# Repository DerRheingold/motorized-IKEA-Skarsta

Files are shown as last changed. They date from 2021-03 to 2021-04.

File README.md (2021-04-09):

# motorized-IKEA-Skarsta

## The idea
The basic idea behind this was relatively simple: After the crank of my desk broke after a few months (the plastic part came lose) I wanted to motorize my Ikea Skarsta desk to automatically raise or lower by the press of a button. After a quick search I found two pages that inspired me and based on them I started putting the things together and modifying the code for the Arduino. As an added challenge: my desk isn't light. I got a water cooled desktop-PC sitting on it together with a Samsung 49" monitor. So I guess it's a total of 35-40 Kg that needs to be moved in total.

## Inspired by:
* http://cesarmoya.com/blog/motorizing-standup-desk/ (for most of the code and parts-list)
* https://github.com/aenniw/ARDUINO/tree/master/skarsta (for the 3d-printing layouts and the idea with sonar + 7-segment display hidden under a layer of 3D-print)

## The required parts (links to German shops):
* [Arduino Uno - 22€](https://www.exp-tech.de/plattformen/plattformen/arduino-plattform/mainboards/4380/arduino-uno-r3)
* [L298N Motor Driver - 4,50€](https://www.ebay.de/sch/i.html?_from=R40&_nkw=L298N&_sacat=0&rt=nc&LH_PrefLoc=1)
* [2 x 24v DC Motors (23kg.cm torque) - 41,65€/piece](https://www.exp-tech.de/motoren/dc-getriebemotoren/9878/50-1-metal-gearmotor-37dx70l-mm-24v-with-64-cpr-encoder-helical-pinion)
* [2 x L-Bracket for Motor - 6,50€](https://www.exp-tech.de/motoren/zubehoer-fuer-motoren/4857/pololu-stamped-aluminum-l-bracket-pair-for-37d-mm-metal-gearmotors)
* [24v 6A AC/DC Adapter - 17€](https://www.ebay.de/itm/Netzteil-Trafo-DC12-24V-2A-10A-Netzadapter-Driver-f-LED-Strip-Streifen-Notebook/224113909308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)
* [Sonar sensor - HC-SR04 - 3€](https://www.ebay.de/sch/i.html?_from=R40&_nkw=HC-SR04&_sacat=0&rt=nc&LH_PrefLoc=1)
* [TM1637 7-Segment-Display with 4 digits 0,56" - 3€](https://www.ebay.de/itm/TM1637-LED-4-Ziffern-7-Segment-Display-Uhr-Arduino-Raspberry/203030439344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)
* [2 x Motor Shaft Coupling (6mm to 7mm) - 3€/piece](https://www.ebay.de/sch/i.html?_from=R40&_nkw=Wellenkupplung+6mm&_sacat=0&rt=nc&LH_PrefLoc=1)
* 4x Push Buttons
* 8x 8mm washers
* 4x 10k OHM Resistors
* Barrel Jack to Cable adapter
* Junction Box
* Solderless Breadboard
* a hand full of jumper wires (Male-Female, as well as Male-Male)
* a friend with a 3D printer 😉
* some time to do metal working on the original drive shaft

Total cost ± 140€ depending on what small parts you have at home anyway.
Links to the shops are no ads, just to the parts I ordered and made some good experience with.

## The setup
Cut the crank apart if you want to, or use another 6mm allen wrench that you can get to fit. I recommend using a 7mm shaft coupling for easiest fit.

## The wiring
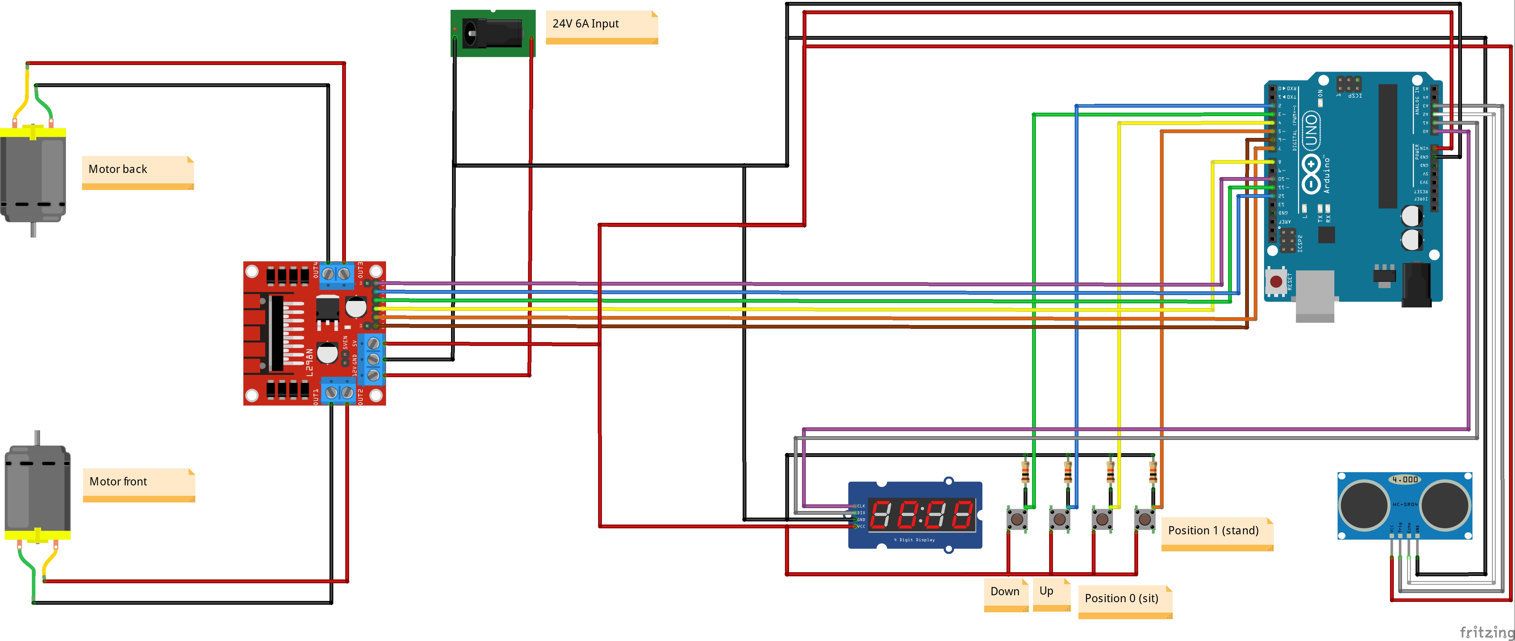
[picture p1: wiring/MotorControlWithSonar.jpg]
Wiring for the Ikea Skarsta project


## First run
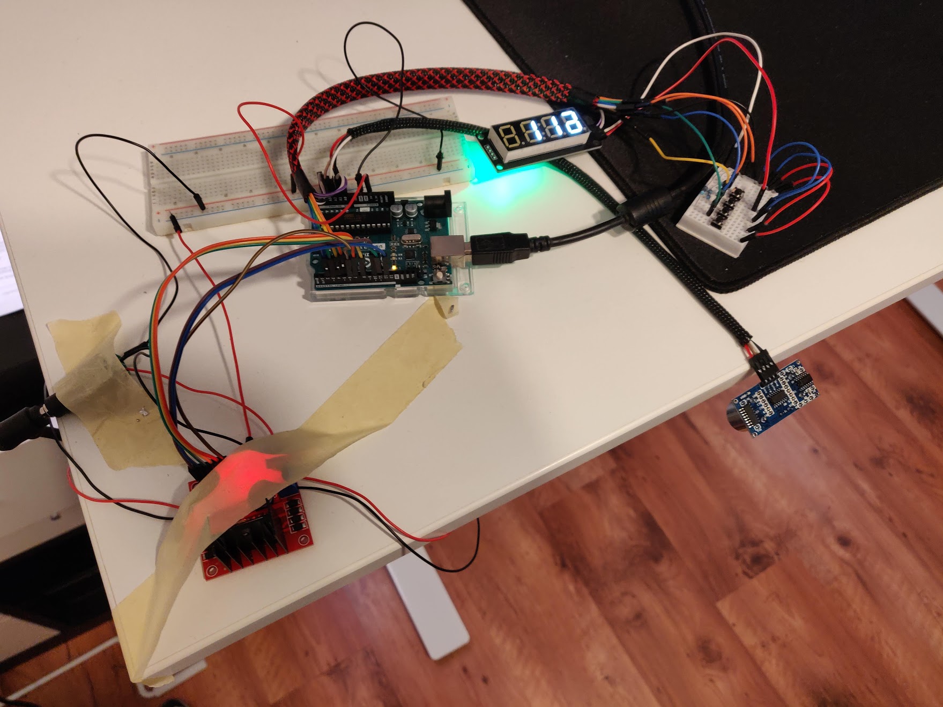
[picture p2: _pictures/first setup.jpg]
First setup of the system

Install everything outside of the desk first. When you're sure that everything is complete and the motors turn correctly install them under your desk. Make sure to measure trice and screw in only once 😉 Between the table and the L-Bracket holding the motors I installed 3mm washers to get the motor into the correct height aligned to the drive shaft. 

Once the motors are installed under the table, keep the wiring and Arduino-parts on the table to make a dry run. This will make debugging the software easier. Also Have a look at the Serial Monitor output when it's running, that might help finding errors too.

Remember to unplug the 5V-Pin in the arduino if you're running the external power to the peripherals and have the arduino plugged in to your PC via USB.

## 3D print
A friend and colleague of mine was so kind to assist my project when it came to the part of 3D printing. Based on the files provided he shortened the panel to house the display and 4 buttons: up, down, 0 and 1.

Also the housing for the sonar sensor was printed. Yes we could have made some housing to fit sonar, display and buttons in one pice. That's maybe something for a future update 😉

## Problems encountered and solved
* Voltage: First I tried with a 29V 2A power supply. This didn't provide enough "ompf" to let the motors drive the desk up. It only wen down 🙄 After upgrading to a 24V 6A power supply it worked fine. Though the L298N only outputs 18-19V to the motors the current is strong enough to power the motors. After all they are rated with 3A per motor :)
* NewPing: Initially it worked fine and just as intended. However when I didn't provide USB-power anymore but used an external power supply I constantly got errors. Turns out it's somewhat of [a known issue with newPing](https://arduino.stackexchange.com/questions/17406/ultrasonic-sensor-returns-random-values-on-external-power-supply). So I migrated to "Ultrasonic" which works fine now 😊

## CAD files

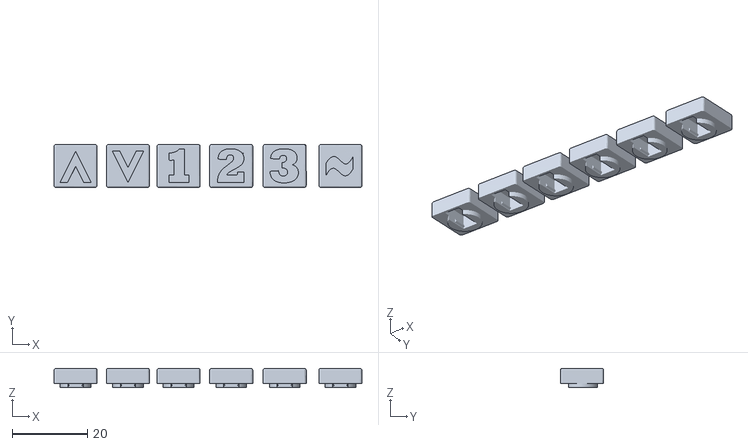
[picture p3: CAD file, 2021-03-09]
3d print/buttons.stl
82.0 x 11.5 x 5.17

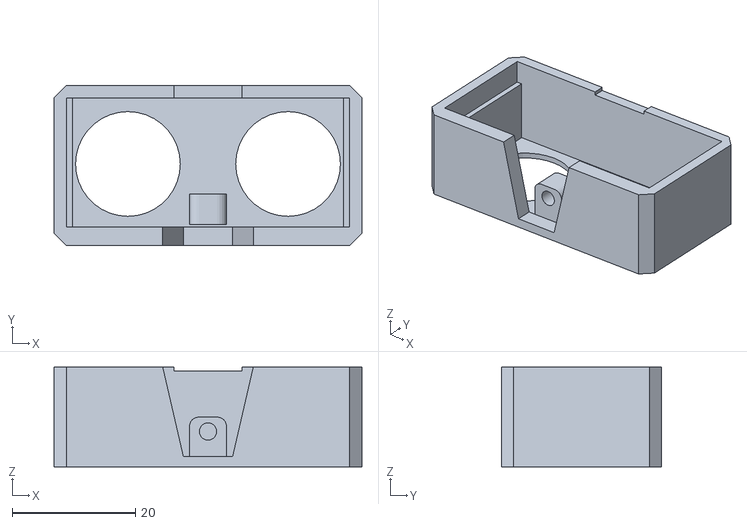
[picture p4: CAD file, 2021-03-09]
3d print/sonar-cap.stl
50.0 x 26.0 x 16.2

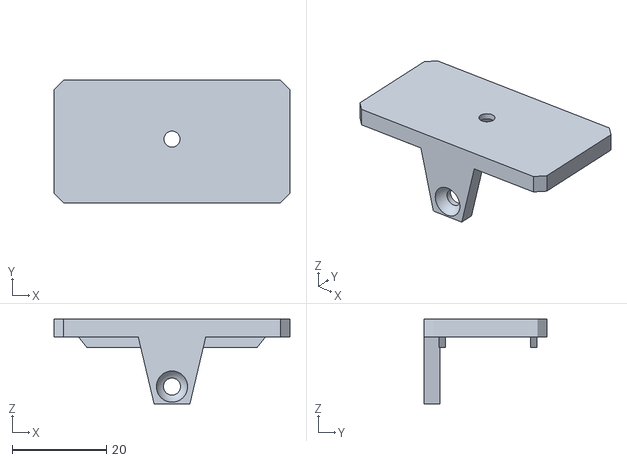
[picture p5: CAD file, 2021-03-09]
3d print/sonar-mount.stl
50.0 x 26.0 x 17.9

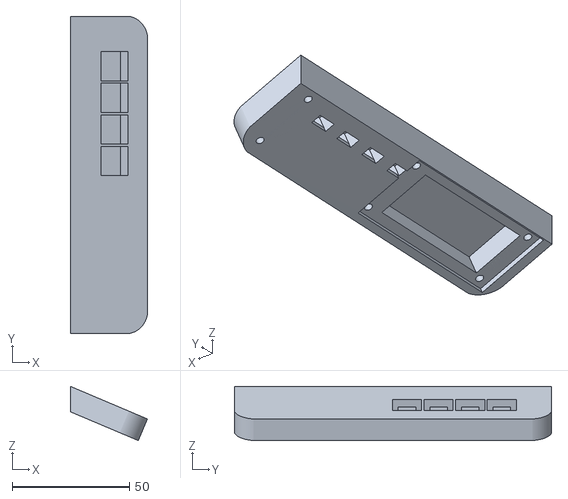
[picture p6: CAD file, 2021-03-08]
3d print/panel-cover-small.stl
32.9 x 135.4 x 23.1

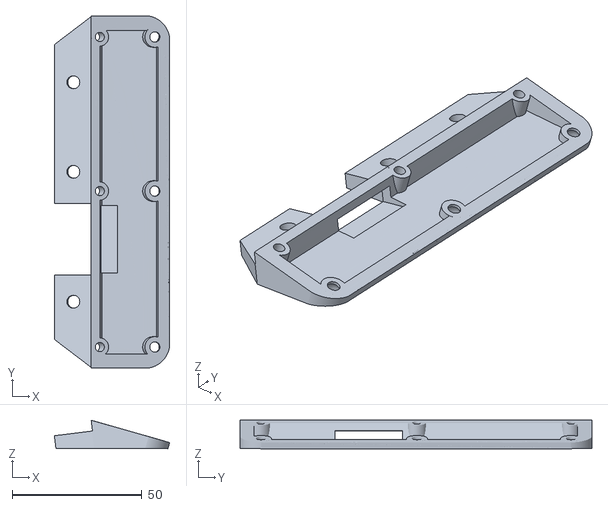
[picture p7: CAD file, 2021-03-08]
3d print/panel-bottom-small.stl
44.4 x 135.4 x 11.0

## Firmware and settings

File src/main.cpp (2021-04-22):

/*
  ----------------------------
   Arduino Power Desktop PLUS
  ----------------------------
  SUMMARY 
    Controls the direction and speed of the motor, supports auto-raising and auto-lowering by measuring the distance via sonar sensor
  
  DESCRIPTION 
    This code waits for a button to be pressed (UP or DOWN), and accordingly powers the motors in the desired direction and speed.
    One motor will turn clockwise, the other counterclockwise. The motors are intended to be placed facing each other, to duplicate the torque on the allen wrench
    On my particular setup (a heavy water cooled tower-PC and one 49" monitor totaling around 35-40 kg) I use 100% of the power speed and torque when raising the desk,
    however, when lowering the desk I need a bit less since gravity helps, to keep the speed up and down at a similar rate, this is configurable.
    You may want to tweak the variables PWM_SPEED_UP and PWM_SPEED_DOWN to adjust it to your desktop load, the allowed values
    are 0 (min) to 255 (max).

  BASIC USAGE
    - Press and hold BUTTON_UP to raise the desk. a small delay of 250ms has been introduced for smoothness
    - Press and hold BUTTON_DOWN to lower the desk. a small delay of 250ms has been introduced for smoothness
    - Press and hold the "Position 0" button to save the lower/sitting position
    - Press and hold the "Position 1" button to save the higher/standing position
    - Press the "Position 0" button shortly to automatically have the desk drive into this position. It stops as soon as the sonar sensor reads the distance from the ground is equal or lower than saved
    - Press the "Position 1" button shortly to automatically have the desk drive into this position. It stops as soon as the sonar sensor reads the distance from the ground is equal or higher than saved
    - The desk should also automatically stop as soon as there is an error in the sonar reading

  ERROR CODES
    Err0: When trying to save a sitting position that is HIGHER than a standing position "Err0" will be shown in the display
    Err1: When trying to save a standing position that is LOWER than a sitting position "Err1" will be shown in the display
    Err2: If there is an error in the sonar (be it while manually or automatically moving the desk) "Err2" is shown in the display. The automatic program will stop directly. Manual adjustment is still possible.


  You may use this code and all of the diagrams and documentations completely free. Enjoy!

  CREDITS
  - https://github.com/cesar-moya/arduino-power-desktop <-- most of the code
  - https://github.com/aenniw/ARDUINO/tree/master/skarsta <-- idea with the 7-segment display and 3d-print files
  
  Original Author:  Cesar Moya
             Date:  July 28th, 2020
              URL:  https://github.com/cesar-moya/arduino-power-desktop
  Updated by:       https://github.com/DerRheingold/motorized-IKEA-Skarsta
*/
#include <EEPROM.h>
#include <Arduino.h>
#include <TM1637Display.h>
#include <Ultrasonic.h>

/* TO DO
- 
*/

#define BUTTON_UP 2     
#define BUTTON_DOWN 3   
#define BUTTON_POS_0 4  
#define BUTTON_POS_1 5  
#define enA 6           
#define in1 7           
#define in2 8           
#define enB 10          
#define in3 11          
#define in4 12          
#define CLK 14          // 7 Segment
#define DIO 15          // 7 Segment
#define ECHO_PIN 16     // Arduino pin tied to echo pin on the ultrasonic sensor
#define TRIGGER_PIN 17  // Arduino pin tied to trigger pin on the ultrasonic sensor

Ultrasonic ultrasonic(TRIGGER_PIN, ECHO_PIN);
TM1637Display display(CLK, DIO);

// Definitions for Platformio
void readFromEEPROM();
void handleButtonUp();
void handleButtonDown();
void position_0();
void position_1();
void checkHeight();
void goDown();
void goUp();
void stopMoving();

//Struct to store the various necessary variables to persist the autoRaise/autoLower programs to EEPROM
struct StoredProgram
{
  int pos0Height = 0; //height in cm above ground for the sitting position
  int pos1Height = 0; //height in cm above ground for the standing position
};

StoredProgram savedProgram;
int EEPROM_ADDRESS = 0;
int BUTTON_UP_STATE = LOW;
int BUTTON_DOWN_STATE = LOW;
int BUTTON_POS_0_STATE = LOW;
int BUTTON_POS_1_STATE = LOW;
long BUTTON_WAIT_TIME = 250; //the small delay before starting to go up/down for smoothness on any button

//Using custom values to ensure no more than 24v are delivered to the motors given my desk load.
//feel free to play with these numbers but make sure to stay within your motor's rated voltage.
const int PWM_SPEED_UP = 255; //0 - 255, controls motor speed when going UP
const int PWM_SPEED_DOWN = 220; //0 - 255, controls motor speed when going DOWN

// Required for additional buttons
long pressedTime;
long releasedTime;
long TimePressed;
const int LONG_PRESS_TIME  = 2000; // The time button "0" or "1" need to be pressed to register as a "long" press to save the current position to eeprom.

// Required for the ultrasonic sensor
int old_Height;
int current_height = 0;
int pos0_height = 0;
int pos1_height = 0;
int digitPosition = 0;

// Some digits/figures for the display
const uint8_t P[] = {
  SEG_A | SEG_B | SEG_E | SEG_F | SEG_G, // P
};
const uint8_t Zero[] = {
  SEG_A | SEG_B | SEG_C | SEG_D | SEG_E | SEG_F, // 0
};
const uint8_t One[] = {
  SEG_B | SEG_C, // 1
};
const uint8_t Two[] = {
  SEG_A | SEG_B | SEG_G | SEG_E | SEG_D, // 2
};
const uint8_t E[] = {
  SEG_A | SEG_D | SEG_E | SEG_F | SEG_G, // E
};
const uint8_t R[] = {
  SEG_E | SEG_G, // r
  SEG_E | SEG_G, // r
};
const uint8_t Minus[] = {
  SEG_G  // -
};
const uint8_t smallO [] = {
  SEG_C | SEG_D | SEG_E | SEG_G // o
};
const uint8_t circle [] = {
  SEG_A | SEG_B | SEG_F | SEG_G  // ° 
};
const uint8_t empty[] = {0x0}; //blank segment for 7-Segment display

//This function debounces the initial button reads to prevent flickering
bool debounceRead(int buttonPin, bool state)
{
  bool stateNow = digitalRead(buttonPin);
  if (state != stateNow)
  {
    delay(10);
    stateNow = digitalRead(buttonPin);
  }
  return stateNow;
}

void animation (const uint8_t* symbol, int delayTime){
  int digitPosition = 0;
  while (digitPosition <  4 ){  
    delay (delayTime);
    display.setSegments (symbol,1,digitPosition);
    digitPosition++;
    if (digitPosition >= 4){
      break;
    }
  };
}

void showOnDisplay (const uint8_t* firstChar, const uint8_t* secondChar, const uint8_t* thirdChar, const uint8_t* fourthChar){
  display.setSegments (firstChar,1,0);  
  display.setSegments (secondChar,1,1);
  display.setSegments (thirdChar,1,2);
  display.setSegments (fourthChar,1,3);
}

void setup() {
  Serial.begin(9600);
  pinMode(LED_BUILTIN, OUTPUT);
  pinMode(BUTTON_DOWN, INPUT);
  pinMode(BUTTON_UP, INPUT);
  pinMode(BUTTON_POS_0, INPUT);
  pinMode(BUTTON_POS_1, INPUT);
  pinMode(enA, OUTPUT);
  pinMode(in1, OUTPUT);
  pinMode(in2, OUTPUT);
  pinMode(enB, OUTPUT);
  pinMode(in3, OUTPUT);
  pinMode(in4, OUTPUT);
  readFromEEPROM();
  display.setBrightness(7);
  display.clear();
  //Some start-up-animation on Display
  animation (smallO, 100);
  animation (circle, 100);
  animation (Zero, 100);
  animation (empty, 100);
  display.clear();
  delay (400);
  // Display the saved Position 0 height on the display upon startup
  showOnDisplay (P, empty, Zero, empty);
  delay (1000);
  display.showNumberDec(pos0_height, false);
  delay (1500);
  display.clear();
  delay (400);
  // Display the saved Position 1 height on the display upon startup
  showOnDisplay (P, empty, One, empty);
  delay (1000);
  display.showNumberDec(pos1_height, false);
  delay (1500);
  display.clear();
  delay (400);
  // Display the current height on the display upon startup
  checkHeight(); 
  delay (1500);  
  display.clear();
}

void loop() {
  //Handle press and hold of buttons to raise/lower, and check if enter auto-raise and auto-lower
  handleButtonUp();
  handleButtonDown();

  //Handle press and hold of buttons to drive into a saved position (short press) or to save the current position (long press)
  position_0();
  position_1();
}

/***********************************************
  Pressing the Button for Position 0 (sitting)
  Upon a short press, the table will drive into the lower (sitting) position
  When long-pressed there is a small animation in the display and afterwards (upon release of the button) the current height is saved to eeprom and shown in the display
***********************************************/
void position_0 (){
   bool btnUpState = digitalRead(BUTTON_UP);
   bool btnDownState = digitalRead(BUTTON_DOWN);
   bool btnPos0State = digitalRead(BUTTON_POS_0);
   int digitPosition = 0;
   current_height = ultrasonic.read();
   if (BUTTON_POS_0_STATE==LOW && debounceRead(BUTTON_POS_0, BUTTON_POS_0_STATE)){  //define what to do when the button is pressed 
       BUTTON_POS_0_STATE=HIGH;
       Serial.println("BUTTON Position 0 Pressed");
       pressedTime = millis(); 
       while (btnPos0State && debounceRead(BUTTON_POS_0, BUTTON_POS_0_STATE)){  //small animation on Display while button is held down longer than 500 ms
         delay (400);
         display.setSegments (smallO,1,digitPosition);
         digitPosition++;
         if (digitPosition >= 4){
          delay (400);
          showOnDisplay (Zero, Zero, Zero, Zero);
          break;
          }
        }
      }
   else if (BUTTON_POS_0_STATE==HIGH && !debounceRead(BUTTON_POS_0, BUTTON_POS_0_STATE)){ //releasing the button checks how long it was pressed and then decides what to do
       BUTTON_POS_0_STATE=LOW;
       releasedTime = millis();   
       TimePressed = releasedTime-pressedTime;

       //If "Position 0 button" is long-pressed, save current height to Position 0, display "P 0" and the height in cm in the display
       if (TimePressed >= LONG_PRESS_TIME){  
        int pos0SaveHeight = ultrasonic.read();
        pos1_height = savedProgram.pos1Height;
        if (pos0SaveHeight >= pos1_height) {  //Check if Position 0 is lower than Position 1. If not, display "Err0"
          Serial.print ("must be lower than "); 
          Serial.println (pos1_height);
          showOnDisplay (E, R, R, Zero);
          delay (1000);
          display.clear();
        }
        else { // Save height and give output to user
          savedProgram.pos0Height = pos0SaveHeight;
          EEPROM.put(EEPROM_ADDRESS, savedProgram);
          Serial.print("Saved Position 0: ");
          Serial.println(pos0SaveHeight);
          showOnDisplay (P, empty, Zero, empty);
          delay (1000);
          display.showNumberDec(pos0SaveHeight, false);
          delay (1000);
          display.clear();
        };          
       }
         
       if (TimePressed < LONG_PRESS_TIME){  //If "Position 0 button" is short-pressed, check height and if possible drive to desired height
        showOnDisplay (P, empty, Zero, empty);
        delay (100);
        int desired_height = pos0_height;
        if (current_height == 0){ //Catch Sonar-Error before starting program
          Serial.println("Won't start Down-Program because of Sonar Error.");
        };
        while (current_height > desired_height){
          checkHeight();
          Serial.print ("desired: "); Serial.println(desired_height);
          goDown();
          if (current_height <= desired_height && current_height != 0){ //stop automatically if the desired height is reached
            delay (500); //a short delay to compensate for sensor inaccuracy.
            stopMoving();
            Serial.println("Sitting position reached");
            showOnDisplay (P, empty, Zero, empty);
            delay (1000);
            checkHeight();
            break;
          }
          else if (current_height == 0){  //Catch Sonar-Error while table is moving and abort program
            Serial.println("Sonar Error in automated down-program");
            checkHeight();
            break;
          }
          if(!btnUpState && debounceRead(BUTTON_UP, btnUpState)){    //Cancel if up- or down-button is pressed during automatic procedure
            stopMoving();
            Serial.println("Program cancelled by user, BUTTON UP");
            animation (Minus, 50);
            break;
          }
          else if(btnUpState && !debounceRead(BUTTON_UP, btnUpState)){
            btnUpState = LOW;
          }
      
          if (!btnDownState && debounceRead(BUTTON_DOWN, btnDownState)){
            stopMoving();
            Serial.println("Program cancelled by user, BUTTON DOWN");
            animation (Minus, 50);
            break;
          }
          else if (btnDownState && !debounceRead(BUTTON_DOWN, btnDownState)){
            btnDownState = LOW;
          }
        };
        Serial.println("End Down-Program");
        stopMoving();
        delay (500);
        checkHeight();
        delay (1500);
        display.clear();
       };
   };
};


/**********************************************
  Pressing the Button for Position 1 (standing)
  Upon a short press, the table will drive into the higher (standing) position
  When long-pressed there is a small animation in the display and afterwards (upon release of the button) the current height is saved to eeprom and shown in the display
***********************************************/
void position_1 (){
   bool btnUpState = digitalRead(BUTTON_UP);
   bool btnDownState = digitalRead(BUTTON_DOWN);
   bool btnPos1State = digitalRead(BUTTON_POS_1);
   int digitPosition = 0;
   current_height = ultrasonic.read();
    if (BUTTON_POS_1_STATE==LOW && debounceRead(BUTTON_POS_1, BUTTON_POS_1_STATE)){ //define what to do when the button is pressed 
       BUTTON_POS_1_STATE=HIGH;
       Serial.println("BUTTON Position 1 Pressed");
       pressedTime = millis(); 
       while (btnPos1State && debounceRead(BUTTON_POS_1, BUTTON_POS_1_STATE)){  //small animation on Display while button is pressed
         delay (400);
         display.setSegments (smallO,1,digitPosition);
         digitPosition++;
         if (digitPosition >= 4){
          delay (400);
          showOnDisplay (Zero, Zero, Zero, Zero);
          break;
         }
       }
      }
   else if (BUTTON_POS_1_STATE==HIGH && !debounceRead(BUTTON_POS_1, BUTTON_POS_1_STATE)){ //releasing the button checks how long it was pressed and then decides what to do
       BUTTON_POS_1_STATE=LOW;
       releasedTime = millis();   
       TimePressed = releasedTime-pressedTime;

       //If "Position 1 button" is long-pressed, save current height to Position 1 and display "P 1" and the height in cm in the display
       if (TimePressed >= LONG_PRESS_TIME){ 
        int pos1SaveHeight = ultrasonic.read();
        pos0_height = savedProgram.pos0Height;
        if (pos1SaveHeight <= pos0_height) {  //Check if Position 1 is higher than Position 0. If not, display "Err1"
          Serial.print ("must be higher than "); 
          Serial.println (pos0_height);
          showOnDisplay (E, R, R, One);
          delay (1000);
          display.clear();
        }
        else { // Save height and give output to user
          savedProgram.pos1Height = pos1SaveHeight;
          EEPROM.put(EEPROM_ADDRESS, savedProgram);
          Serial.print("Saved Position 1: ");
          Serial.println(pos1SaveHeight);
          showOnDisplay (P, empty, One, empty);
          delay (1000);
          display.showNumberDec(pos1SaveHeight, false); 
          delay (1000);
          display.clear();
        }        
       }
       
       if (TimePressed < LONG_PRESS_TIME){ //If "Position 1 button" is short-pressed, check height and if possible drive to desired height
        showOnDisplay (P, empty, One, empty);
        delay (100);
        int desired_height = pos1_height;
        if (current_height == 0){ //Catch Sonar-Error before starting program
          Serial.println("Won't start Up-Program because of Sonar Error.");
        };
        while (current_height < desired_height && current_height != 0){
          checkHeight();
          Serial.print ("desired: "); Serial.println(desired_height);
          goUp();
          if (current_height >= desired_height){ //stop automatically if the desired height is reached
            delay (500); //a short delay to compensate for sensor inaccuracy.
            stopMoving();
            Serial.println("Standing position reached");
            showOnDisplay (P, empty, One, empty);
            delay (1000);
            checkHeight();
            break;
          }
          else if (current_height == 0){  //Catch Sonar-Error while table is moving and abort program
            Serial.println("Sonar Error in automated up-program");
            checkHeight();
            break;
          }
          if(!btnUpState && debounceRead(BUTTON_UP, btnUpState)){    //Cancel if up- or down-button is pressed during automatic procedure
            stopMoving();
            Serial.println("Program cancelled by user, BUTTON UP");
            animation (Minus, 50);
            break;
          }
          else if(btnUpState && !debounceRead(BUTTON_UP, btnUpState)){
            btnUpState = LOW;
          }
      
          if (!btnDownState && debounceRead(BUTTON_DOWN, btnDownState)){
            stopMoving();
            Serial.println("Program cancelled by user, BUTTON DOWN");
            animation (Minus, 50);
            break;
          }
          else if (btnDownState && !debounceRead(BUTTON_DOWN, btnDownState)){
            btnDownState = LOW;
          }
        };
        Serial.println("End Up-Program");
        stopMoving();
        delay (500);
        checkHeight();
        delay (1500);
        display.clear();
       };
   };
};

void showHeightIfChanged() {
  if (current_height != old_Height && current_height != 0) {  //avoid flickering of 7-segment as it now only refreshes if the value has changed
    Serial.print("current height: "); Serial.println(current_height);
    display.showNumberDec(current_height, false);
    old_Height = current_height;
  }
}

void checkHeight() {    // Get Sensor Reading and display on 7-Segment
  display.setBrightness(7);
  current_height = ultrasonic.read();
  showHeightIfChanged();
  if (current_height == 0) { //display "Err2" if the sonar sensor has an error"
    showOnDisplay (E, R, R, Two);
    Serial.println("Sonar Sensor Error");
    };
  delay(100); //polling frequency of the sonar sensor. Not recommended to go below 30-50 ms
}


/****************************************
  MAIN CONTROL FUNCTIONS
****************************************/
//This function takes care of the events related to pressing BUTTON_UP, and only BUTTON_UP. It raises the desk when holding it
void handleButtonUp()
{
  //If button is held the desk raises
  if (!BUTTON_UP_STATE && debounceRead(BUTTON_UP, BUTTON_UP_STATE))
  {
    Serial.println("BUTTON UP Pressed");
    BUTTON_UP_STATE = HIGH;
    long pressTime = millis();
    long elapsed = 0;
    while (digitalRead(BUTTON_UP))
    {
      elapsed = millis() - pressTime;
      Serial.print("BUTTON UP | Holding | elapsed: ");
      Serial.println(elapsed);
      checkHeight();

      //small delay before starting to work for smoothness
      if (elapsed >= BUTTON_WAIT_TIME)
      {
        goUp();
      }

      //If you press down while holding UP, you indicate desire to enter program mode, break the loop to stop going
      //UP, the code will catch the 2 buttons being held separately
      if (debounceRead(BUTTON_DOWN, LOW))
      {
        Serial.println("BUTTON UP | Button DOWN pressed, breaking loop");
        break;
      }
    }
    stopMoving();
  }
  else if (BUTTON_UP_STATE && !debounceRead(BUTTON_UP, BUTTON_UP_STATE))
  {
    Serial.println("BUTTON UP | Released");
    BUTTON_UP_STATE = LOW;
    checkHeight();
    delay(1500);
    display.clear();
  }
}

//This function takes care of the events related to pressing BUTTON_DOWN, and only BUTTON_DOWN. It lowers the desk when holding it
void handleButtonDown()
{
  //If button is held the desk lowers
  if (!BUTTON_DOWN_STATE && debounceRead(BUTTON_DOWN, BUTTON_DOWN_STATE))
  {
    Serial.println("BUTTON DOWN | Pressed");
    BUTTON_DOWN_STATE = HIGH;
    long pressTime = millis();
    long elapsed = 0;
    while (digitalRead(BUTTON_DOWN))
    {
      elapsed = millis() - pressTime;
      Serial.print("BUTTON DOWN | Holding | elapsed: ");
      Serial.println(elapsed);
      checkHeight();

      //small delay before starting to work for smoothness
      if (elapsed >= BUTTON_WAIT_TIME) 
      {
        goDown();
      }

      //If you press UP while holding DOWN, you indicate desire to enter program mode, break the loop to stop going
      //DOWN, the code will catch the 2 buttons being held separately
      if (debounceRead(BUTTON_UP, LOW))
      {
        Serial.println("BUTTON DOWN | Button UP pressed, breaking loop");
        break;
      }
    }
    stopMoving();
  }
  else if (BUTTON_DOWN_STATE && !debounceRead(BUTTON_DOWN, BUTTON_DOWN_STATE))
  {
    Serial.println("BUTTON DOWN | Released");
    BUTTON_DOWN_STATE = LOW;
    checkHeight();
    delay(1500);
    display.clear();
  }
}


/****************************************
  LOWER / RAISE DESK FUNCTIONS
****************************************/
//Send PWM signal to L298N enX pin (sets motor speed)
void goUp()
{
  Serial.print("UP:"); Serial.println(PWM_SPEED_UP);
  digitalWrite(LED_BUILTIN, HIGH);

  //Motor A: Turns in (LH) direction
  analogWrite(enA, PWM_SPEED_UP);
  digitalWrite(in1, LOW);
  digitalWrite(in2, HIGH);

  //Motor B: Turns in OPPOSITE (HL) direction
  analogWrite(enB, PWM_SPEED_UP);
  digitalWrite(in4, HIGH);
  digitalWrite(in3, LOW);
}
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

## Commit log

2021-03-08 Wiring diagram
    [MotorControlWithSonar.fzz]
2021-03-08 Wiring diagram (jpg)
2021-03-08 Updated wiring diagram
    [MotorControlWithSonar.fzz]
2021-03-08 moved wiring into own subdirectory
2021-03-08 Fixing a tyop ;)
    [main.cpp]
2021-03-08 move wiring into directory
    [MotorControlWithSonar.fzz]
2021-03-08 Update README.md
    added part about 3d print
2021-03-08 added 3d-printing files
    [panel-bottom-small.stl, panel-cover-small.stl]
2021-03-09 Added 3d-files from https://github.com/aenniw/
    [sonar-cap.stl, sonar-mount.stl]
2021-03-11 added Ultrasonic and TM1637 library
2021-03-11 Update to the wiring diagram
    [MotorControlWithSonar.fzz]
2021-03-17 bug fix to save-animation
    [main.cpp]
2021-04-22 Fixed typo when saving
    [main.cpp]
